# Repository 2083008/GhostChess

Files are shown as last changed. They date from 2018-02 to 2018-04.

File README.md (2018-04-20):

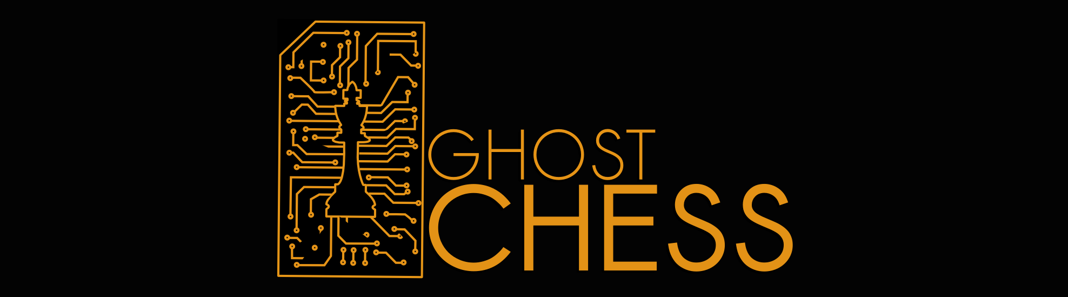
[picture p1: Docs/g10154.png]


Check us out on [Youtube](https://youtu.be/5MZTQNxuwCw) and [HACKADAY](https://hackaday.com/2018/04/19/play-chess-against-a-ghost/)

# team11_RTEP5: Mechanised User vs. Computer Chess Board
Computer chess engines have become very advanced and are great for learning how to play or for improving your skills. However, playing on a computer is just not the same as seeing the physical pieces move across the board!

This project aims to design and build a mechanised chess device, allowing users to play against the StockFish chess engine on a physical board. An X-Y positioning table will use an electromagnet to execute the computer-generated moves, moving the physical pieces across the board, mimicking a real chess expert.

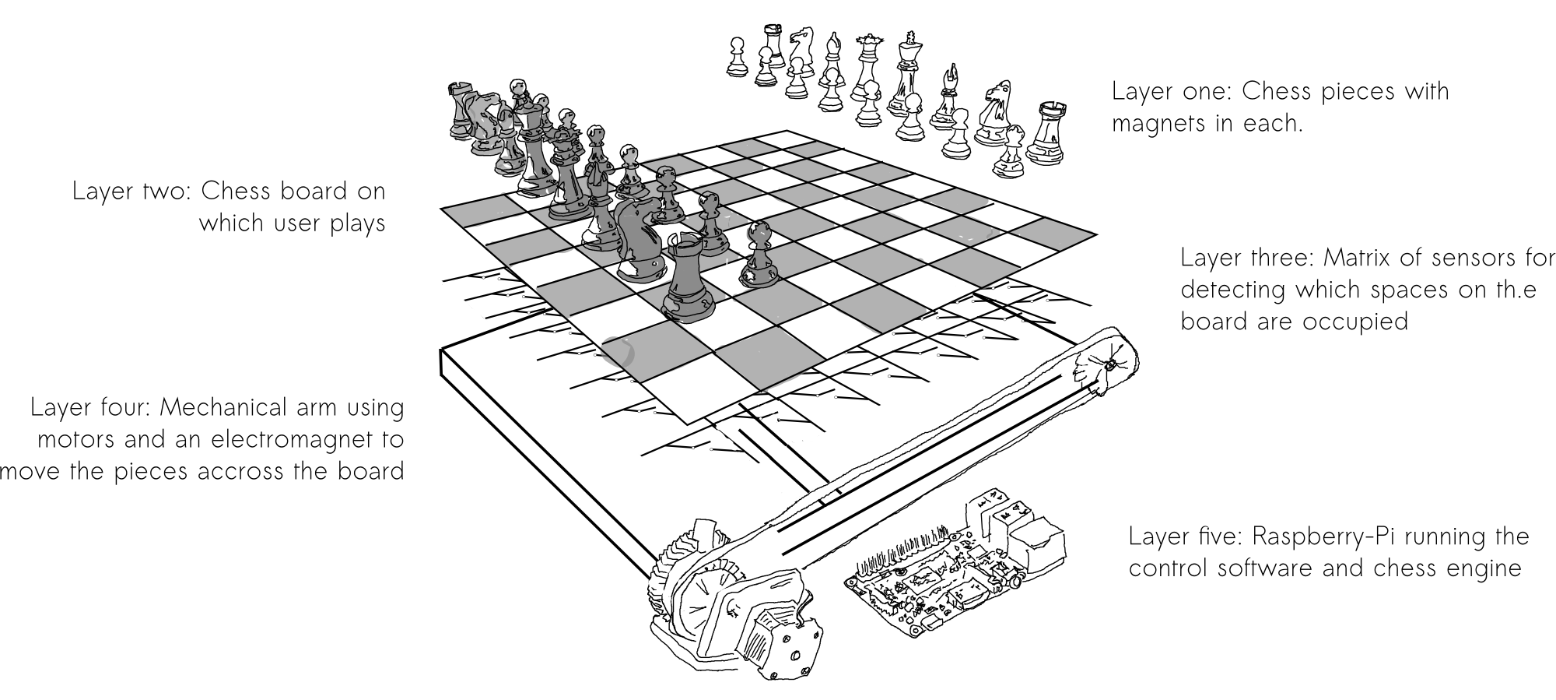
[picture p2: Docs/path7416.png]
Layers of the system


# Why?
Playing games on a computer screen can be great - but it takes away from the game. Ghost Chess allows users to detach from their everyday computer use to really invest in the game itself, providing a more engaging gaming experience. Variable difficulty levels allow users to improve their chess skills. Not to mention that it is really cool!

## Table of Contents
[Getting Started](#getting_started)
  * [Required Hardware](#required_hardware)
  * [Assembling the mechanical arm](#mechanical_arm)
  * [Building Software](#building_software)
  * [Motor Control](#motor_control)
  
[System Specification](#system_specification)

[Project Progress/Evaluation](#progress_evaluation)
  * [Team Roles](#team_roles)

[FAQ/Common Issues](#faq)

# Getting Started 
All project-related software can be found in folder "src", and all required schematics/CAD files/PCB designs/footprints are located in folder "Docs".
## Required Hardware 
* The full [Bill of Materials](goo.gl/mntyCQ): 
X-Y positioning:
* 3x Stepper Motors (Nema 17)
* 3x Stepper motor drivers (Pololu A4988)
* 1x Electromagnet (3/4' Diameter, 4.5kg pull force) and 40x Button Magnets (3mm diameter, 2mm height)
* P36NF06L FET
* 2x 700/900 mm plywood sheets
* 2x 700mm and 1x 500mm T-slot bar
* 3x 125mm oak shuttles
* 6x T-bolts
* 1x 500mm oak bar
* 6x 40T GT2 6mm Timing Pulley
* 5M 6mm GT2 fiber-glass re-enforced rubber timing belt
* 1x 500mm metal shaft and 1x 30mm metal shaft
* 6x Flanged Corner Bracket BZP

Sensor Matrix:
* 64x Latching Hall-effect Sensors (SS361RT) and 64 10kohm resistors
* 2x 8-1 FET Mux/Demux (SN74CBT3251)

Other:
* Laser-cut Acrylic chess board and 3D printed pieces
* Raspberry Pi 3 Model B

# Assembling the mechanical arm: 
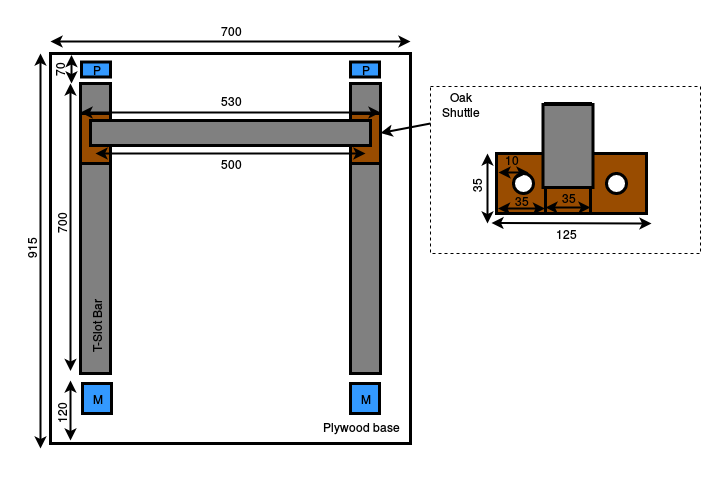
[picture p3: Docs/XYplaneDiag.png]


All measurements in mm.

A Plywood base is used to ensure that there is no unwanted lateral motion under tension. T-slot bars act as runners for oak shuttles, held in place by T-bolts. The Y plane movement is supported by two T-slot bars, each 700mm in length. Mounted to both the Oak shuttles on the Y plane is an oak bar which holds the 3rd, X plane, T-slot bar in place (500mm in length). Each shuttle is moved using a timing belt which is mounted through 2 pulleys to a stepper motor.

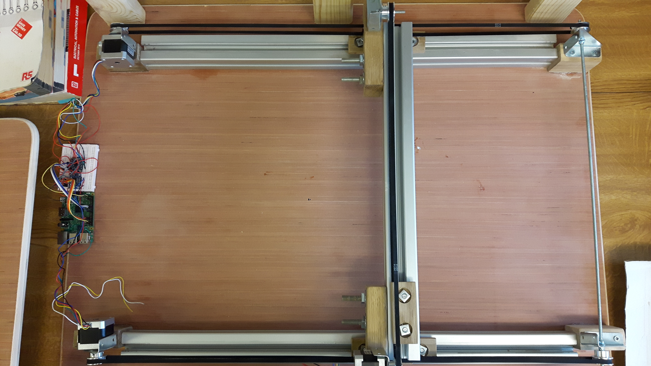
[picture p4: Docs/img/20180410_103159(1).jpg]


1. Cut and bevel the two 915mm/70mm Plywood sheets which form the base and top plate of the design
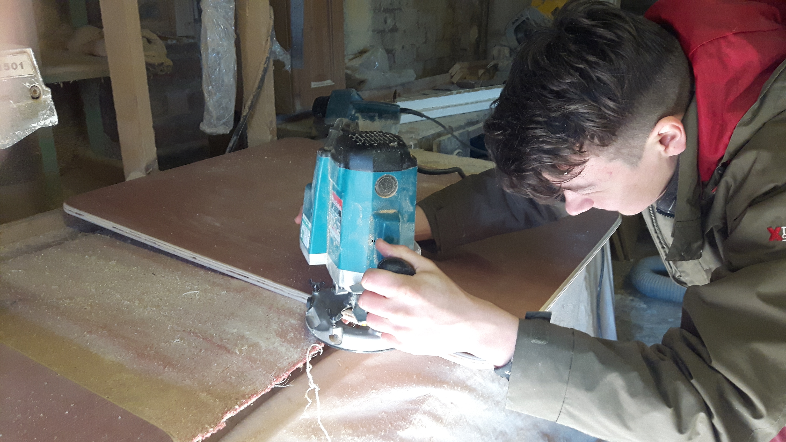
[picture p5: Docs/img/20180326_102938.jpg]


2. Bolt down the 2 700mm length T-slot bars through the base plywood sheet (4 bolts spaced evenly)
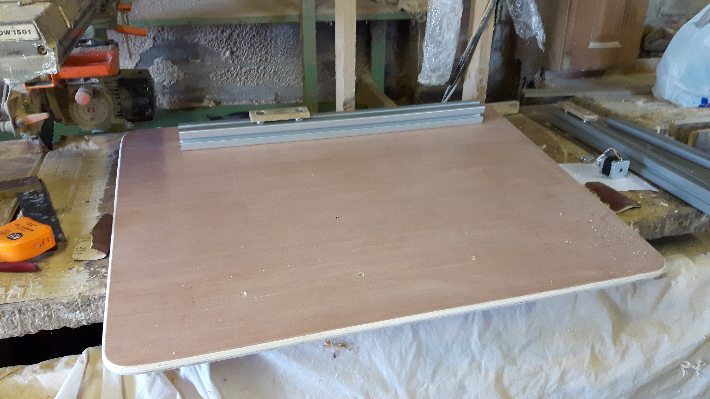
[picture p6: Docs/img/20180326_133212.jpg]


3. Cut the 3 125mm/35mm oak shuttles and the 500mm/35mm oak cross bar
4. Mount the oak cross bar to two of the oak shuttles using miter-fast bond and screws
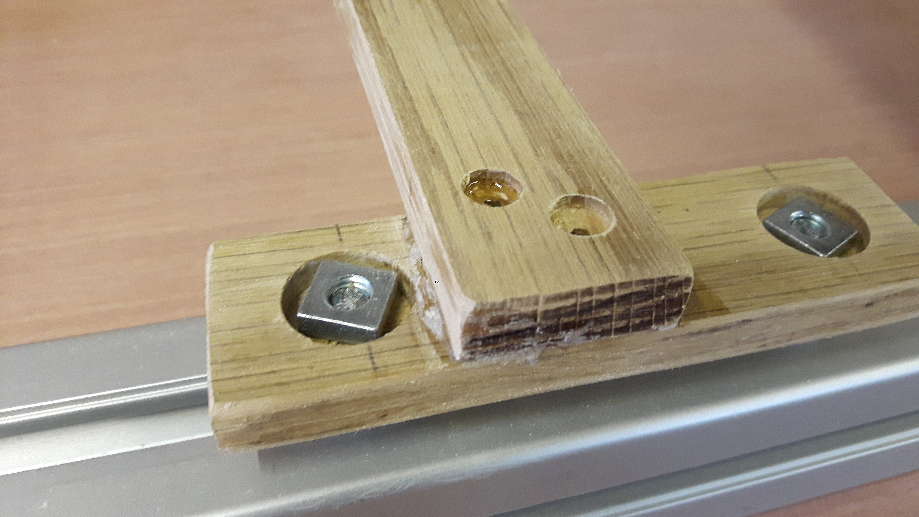
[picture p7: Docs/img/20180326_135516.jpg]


5. Bolt the 500mm T-slot bar to the oak cross bar (4 bolts spaced evenly)
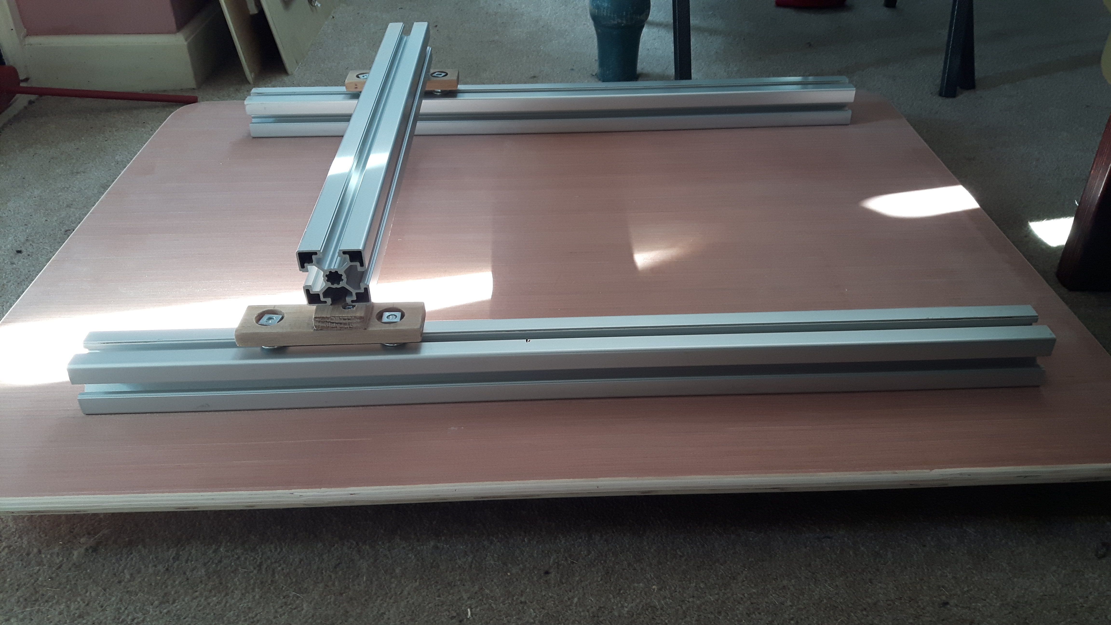
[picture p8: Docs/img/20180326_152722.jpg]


6. Cut oak blocks to stand the pulleys and motors (x6, 3 for motors and 3 for pulleys), plane to match heights (the bottom of the pulleys should be at the same height as the top of the oak shuttles to ensure that the timing belt can be fixed securely)
7. Fix the oak blocks to the plywood base using miter fast bond and screws
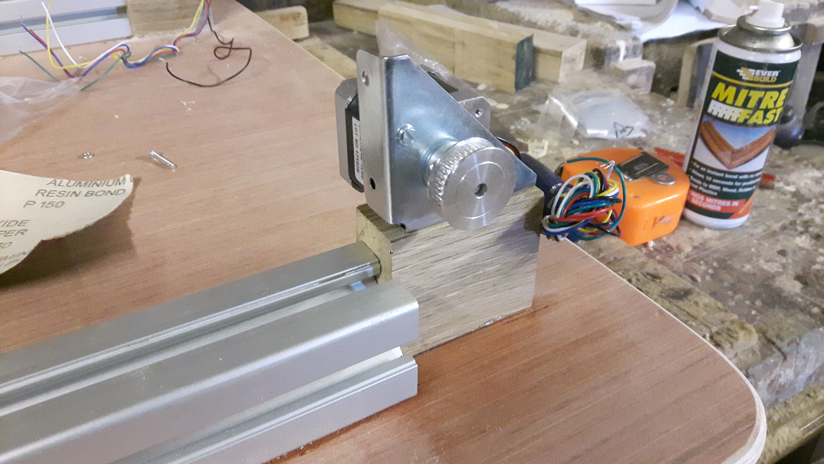
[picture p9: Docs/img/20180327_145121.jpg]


8. fix the flaged corner brackets to the oak blocks, ensuring they are parallel to the T-slot bar and in line
9. attach the motors to the flanged corner brackets by drilling holes in the corner bracket and bolting the motors through them
10. attach pulleys to motor shafts, 500mm metal shaft, and 30mm metal shaft


11. attach timing belt to oak shuttles through pulleys with tension using miter fast bond
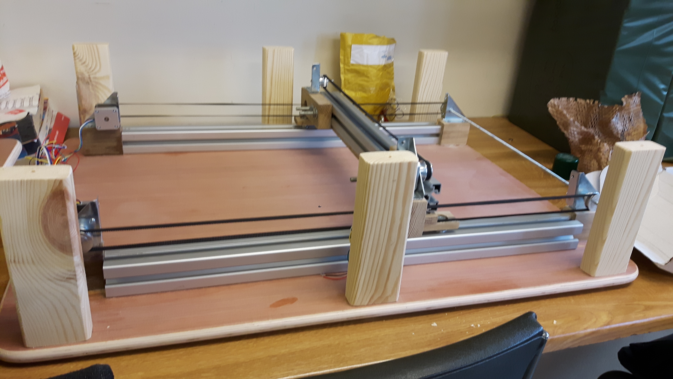
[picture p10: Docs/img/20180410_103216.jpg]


### Electromagnet

The electromagnet is controlled using a GPIO on the RASPI, connected to the gate of a N-Channel FET (P36NF06L) with a R10k to GND. 12V DC from the power supply connected Electromagnet with the other connection to the Drain of the FET and the Source to GND.

# Sensor matrix: detecting the users move
The sensor matrix is comprised of 64 latching (0/1 state will be preserved until reset) hall-effect (detecting magnetic field, turned on by a North magnetic pole and off by South magnetic pole) sensors, with one sensor below each square. The sensor (SS361RT) has three terminals - Supply voltage (V_cc), Output and Ground. The most basic circuit is created by connecting a resistor (10k recommended) between V_cc and Output - the transistor in the sensor would act like a short circuit when turned on (pulling the output to Ground), and as an open circuit when exposed to North magnetic pole (the resistor pulling the output to V_cc or 5V, when supplied from the RaspberryPi). More can be seen in the datasheet: https://sensing.honeywell.com/honeywell-sensing-latching-digital-hall-effect-sensor-ic-datasheet-ss361rt-ss461r-005901-3-en.pdf

To assemble the sensor matrix, follow the steps outlined below. Apart from the components mentioned in the beginning, you will need:
* Solder iron (possibly with a fine tip) and a large amount of solder;
* Long multi and single-core wires;
* Wire strippers;
* Hot glue gun and sticks;
* Cardboard and drawing instruments;
* Duct tape.

1. Copy the exact dimensions of the laser-cut acrylic board and draw lines through all square diagonals, so you find the exact center. Prepare your multi-core wire for the SMD hall-effect sensors:


2. Solder the sensor terminals to wires and start supergluing them to the cardboard, making sure they are positioned exactly in the center:
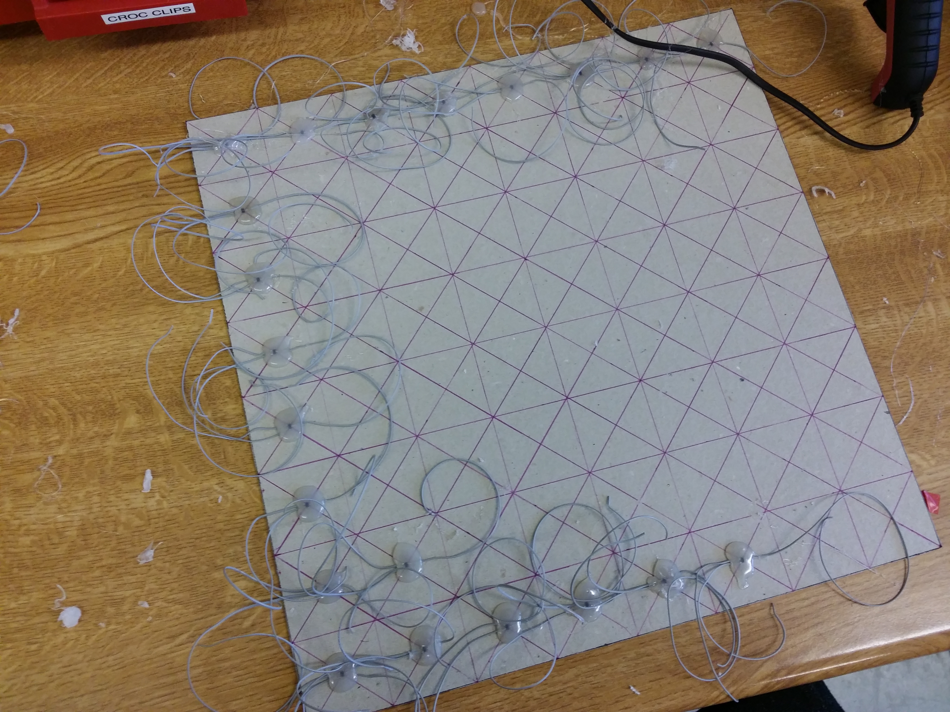
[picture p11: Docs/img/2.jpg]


3. After you have glued all sensors, trim the wires so you have working space:
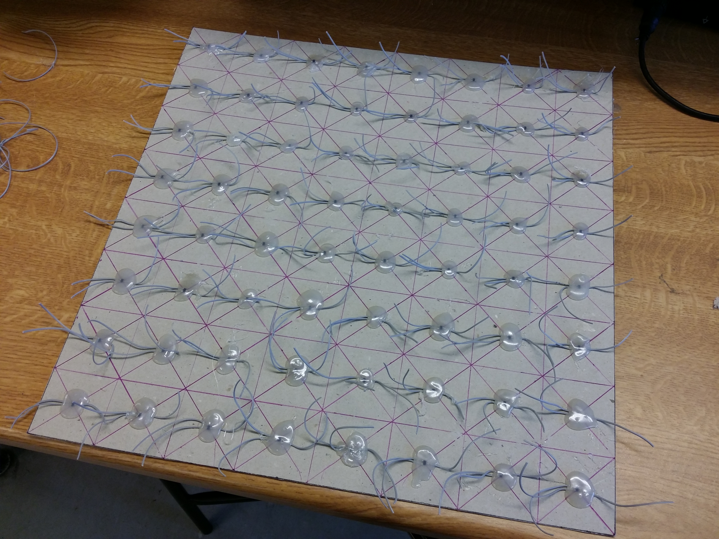
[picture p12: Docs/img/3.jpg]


4. Strip single-core wires, which will serve as "rails". Place them along each column line, starting from the side of the ground terminal. Solder the ground terminal sensor wires to the "ground net".
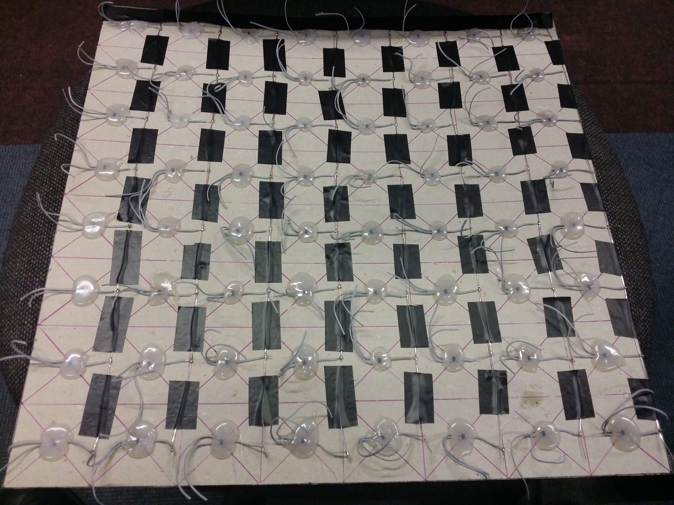
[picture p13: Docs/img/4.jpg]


5. Cover "ground net" with at least 2 layers of duct tape, then place 8 column wires (V_cc) in parallel with the ground wires. Cover the intersections with the rows with duct tape, and place 8 row wires (Output) along the row lines. 


6. Solder the resistors and corresponding sensor wires between the supply and output wire nets:
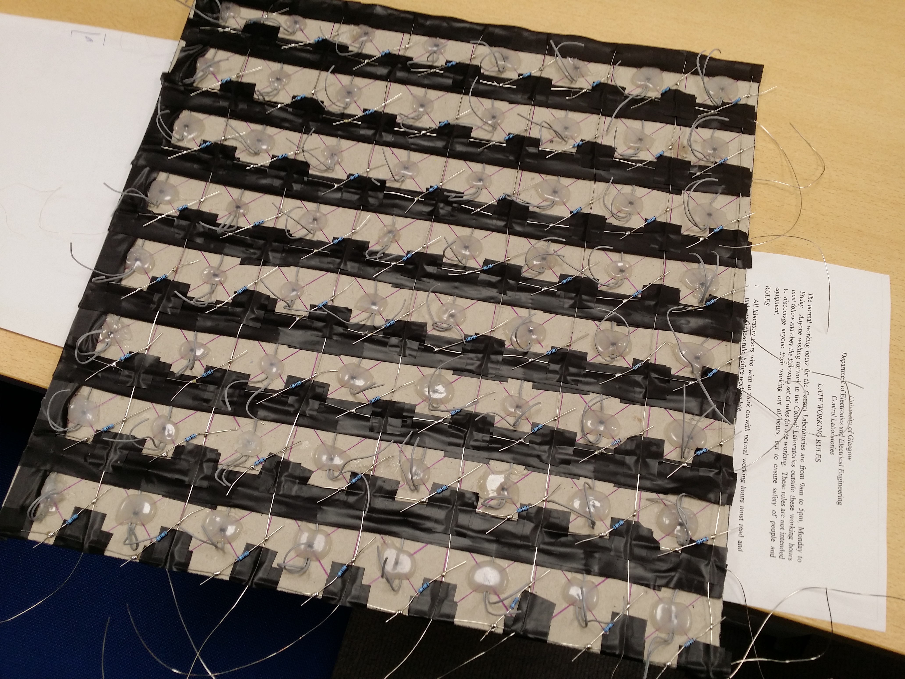
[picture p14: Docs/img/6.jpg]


7. Solder multi-core wires to the two multiplexer/demultiplexers and superglue the sensor, so the SMD legs would not break from bending.
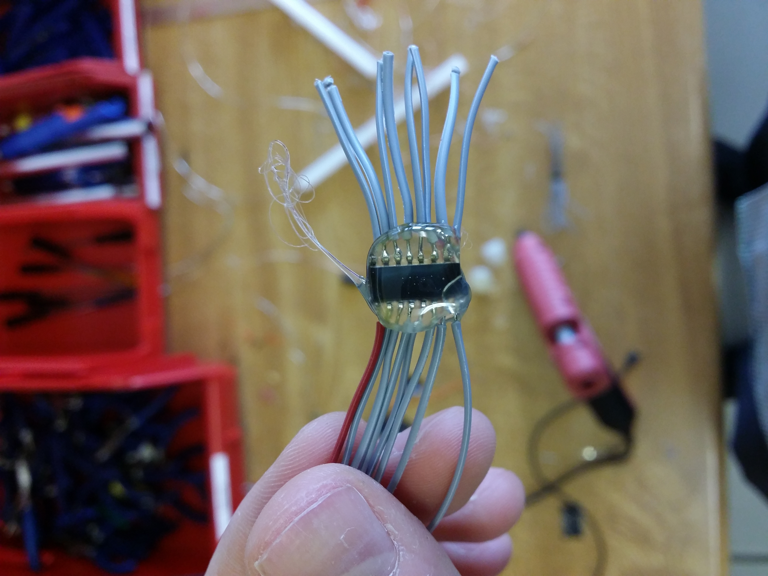
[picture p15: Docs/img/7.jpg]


Prior to connecting everything together, test the output of each hall-effect sensor using a magnet, by iteratively supplying voltage to each column and reading each row. The circuit for the matrix can be seen in Docs/PCB/sensor_array.pdf. Bear in mind that the sensing part of this project is still in alpha.

The Bill of Materials for this project can be seen here: https://docs.google.com/spreadsheets/d/1Xdm7poSaMNww_U4s14YsQG5IgNS09zYjubY1kuaMT44/edit?usp=sharing

# Building Software 
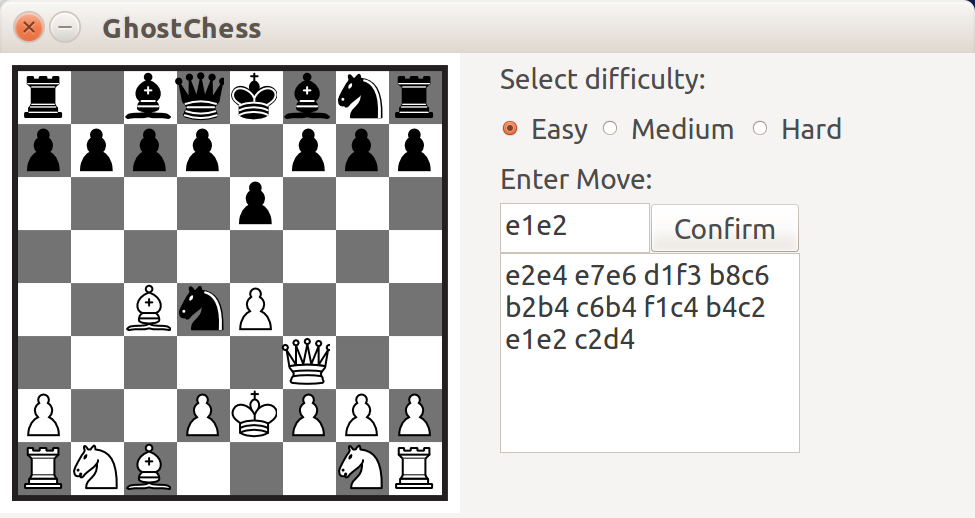
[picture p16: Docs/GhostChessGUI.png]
GUU

To build this project's software: first clone the repository then run

```
cd GhostChess
cmake .
make

./GhostChess

```
**NB** Requires QT5, to install:
```
sudo apt-get install qt-5 default
```
Moves can be entered through the GUI or through the CLI (both entered in Algerbraic Chess Notation eg e2e4...).
## Software Flow:

The software forms an interface between the user and the StockFish API, updating the API with new moves and reading out the computers moves to pass to the motor control software. A full software flow diagram can be found in [Docs/Software_flow_diagram](Docs/Software_flow_diagram.png).

## Motor control: 

Motor control is performed using digital GPIO outputs which control the Pololu A4988 stepper motor driver. The stepper motors are rotated in 4 stages which relates to 4 configurations of the H-bridge inductor which is used to turn the motor shaft. A single rotation therefore relates to:

To move pieces accross the board the control software performs the following steps:
1. Move to coordinate y1 x1 (the coordinate of the piece to be moved)
2. Turn on electro magnet
3. Move to edge of square (to ensure that the peice being moved will not collide with any pieces in surrounding squares)
4. Move to coordinate y2 x2 (the space to be moved to)
5. Return piece to the centre of the square
6. Return to origin of the board (located at square A1)

# System Specification 

Responsiveness of the system. How long the system will take to move a piece.
Latency permitted for the piece -> dependant on where the piece has to move (
Sampling rate of 2Hz for board state of 64 elements.
Thread will poll the board every 2Hz and check for changes/validate and make sure user has moved a piece correctly then the engine will respond.
Bus Protocol, communicating to motor drivers.
Channels? 1
Kernel space usage was not deemed necessary since the latencies were in the order of seconds/ms. For simpicity and faster development time then staying in user space was preferred.
Data flow  is shown in the [software diagram](Docs/Software_flow_diagram.png) (formats, latencies, processing and conversions)
Buffers for the move history of the game as well as the engines returned moves are stored.
 
Threads operate for fetching the user input for the CLI as well. The board array will also be updated using a thread executed at 2Hz.

### Team Roles 
* Alex Angelov - 3D Pieces Modelling, Board Production, Position Sensing and Related Software
* Tim Ness - Design Assembly, Accurate Motor Control and Related Software
* Alex Smith - Chess Engine Integration and QT GUI Interface

# Progress Success Evaluation 
Issue tracking and Project Tracking through github's associated tools.

How does the project acheive the goals that are set out above?

# FAQ/Common Issues 
**Q:** QLabel: No such file or directory

**A:** QT5 must be installed to build the software, run  ```sudo apt-get install qt-5 default ```

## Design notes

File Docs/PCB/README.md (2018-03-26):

THis is the documentation for replicating the PCB created for the GhostChess Project

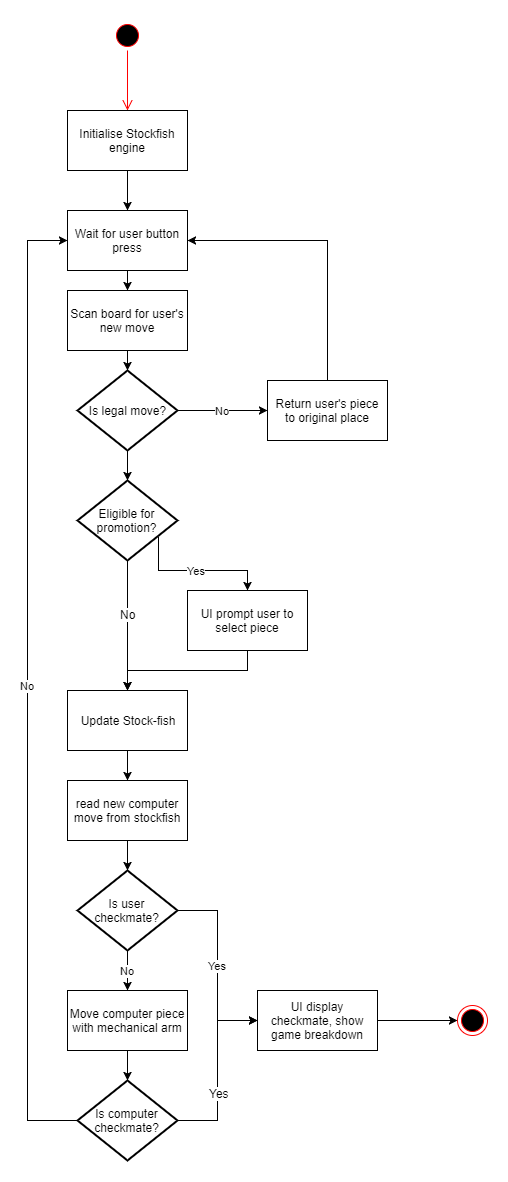
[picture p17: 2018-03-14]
Docs/Software_flow_diagram.png

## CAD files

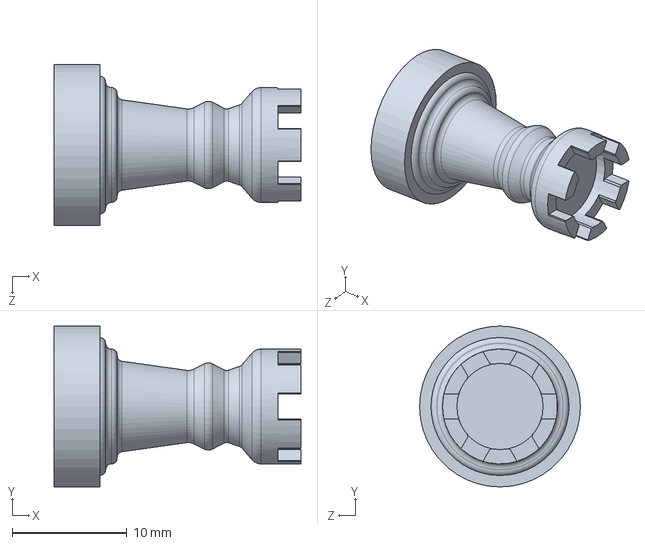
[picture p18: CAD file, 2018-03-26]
Docs/CAD-Mechanical/chess_pieces/ROOK.SLDPRT
21.5 x 14.0 x 14.0 mm

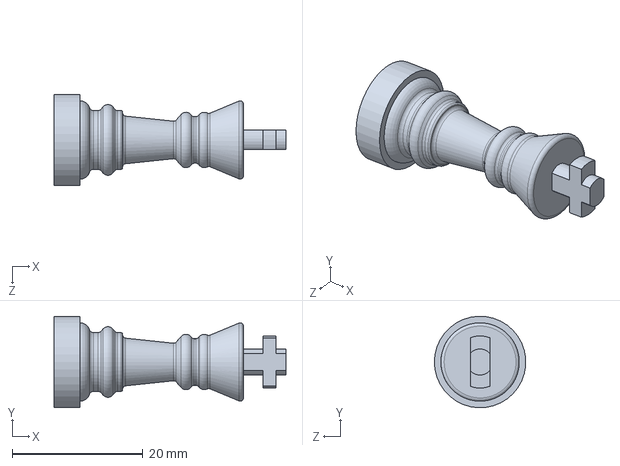
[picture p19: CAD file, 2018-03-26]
Docs/CAD-Mechanical/chess_pieces/KING.SLDPRT
35.5 x 14.0 x 14.0 mm

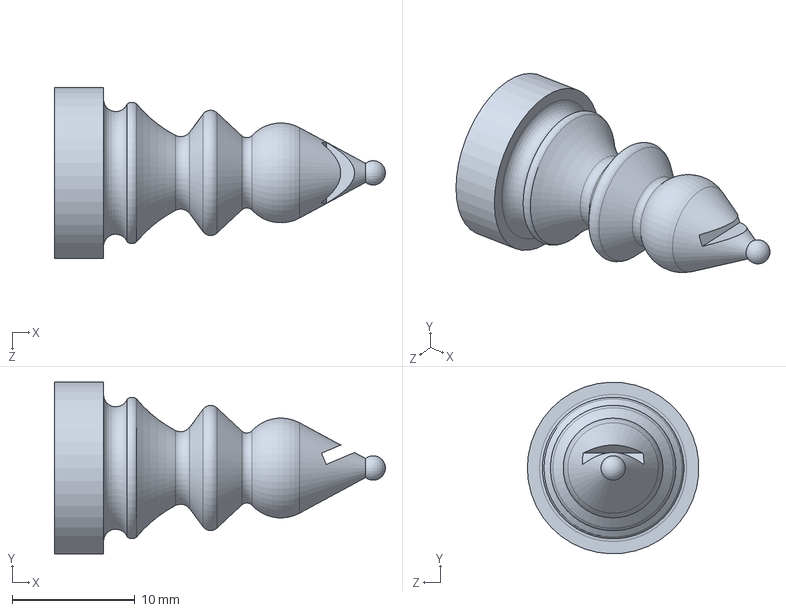
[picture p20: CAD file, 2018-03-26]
Docs/CAD-Mechanical/chess_pieces/BISHOP.SLDPRT
27.0 x 14.0 x 14.0 mm

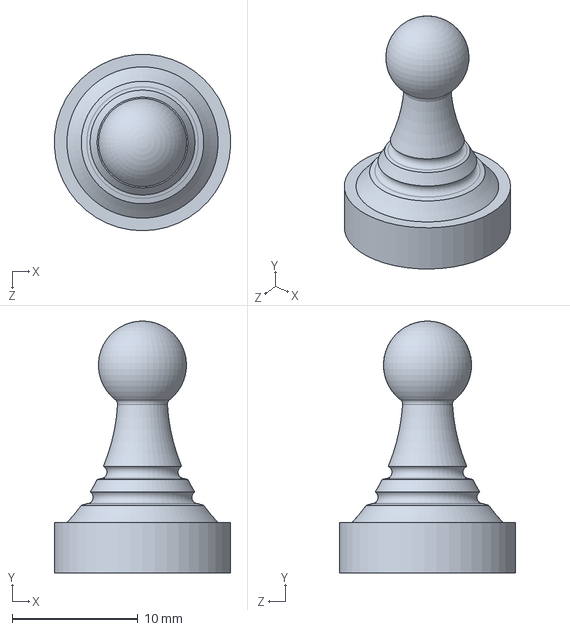
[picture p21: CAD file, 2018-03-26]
Docs/CAD-Mechanical/chess_pieces/PAWN.SLDPRT
14.0 x 20.0 x 14.0 mm

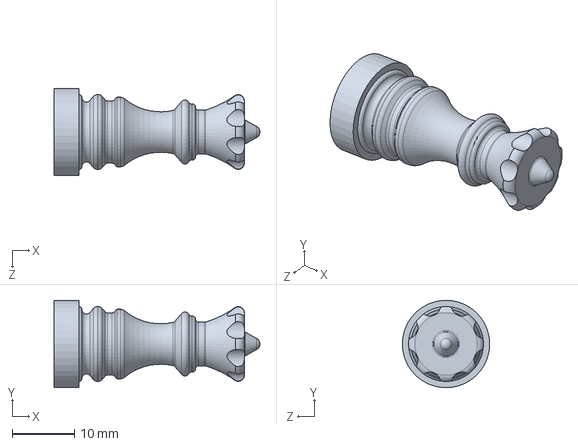
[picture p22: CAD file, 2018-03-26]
Docs/CAD-Mechanical/chess_pieces/QUEEN.SLDPRT
33.0 x 14.0 x 14.0 mm

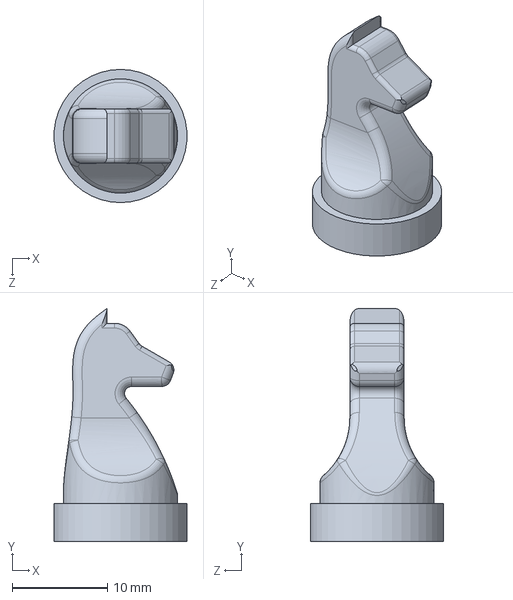
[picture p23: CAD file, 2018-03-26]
Docs/CAD-Mechanical/chess_pieces/KNIGHT.SLDPRT
14.0 x 24.5 x 14.0 mm

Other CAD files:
Docs/CAD-Mechanical/chess_board/chess_board.SLDPRT
Docs/CAD-Mechanical/chess_board/chess_board.DXF
Docs/CAD-Mechanical/chess_pieces/BISHOP.STL
Docs/CAD-Mechanical/chess_pieces/KING.STL
Docs/CAD-Mechanical/chess_pieces/KNIGHT.STL
Docs/CAD-Mechanical/chess_pieces/PAWN.STL
Docs/CAD-Mechanical/chess_pieces/QUEEN.STL
Docs/CAD-Mechanical/chess_pieces/ROOK.STL

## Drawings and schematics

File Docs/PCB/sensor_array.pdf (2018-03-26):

# M2 SN74CBT3251D VCC ¹⁶ GND

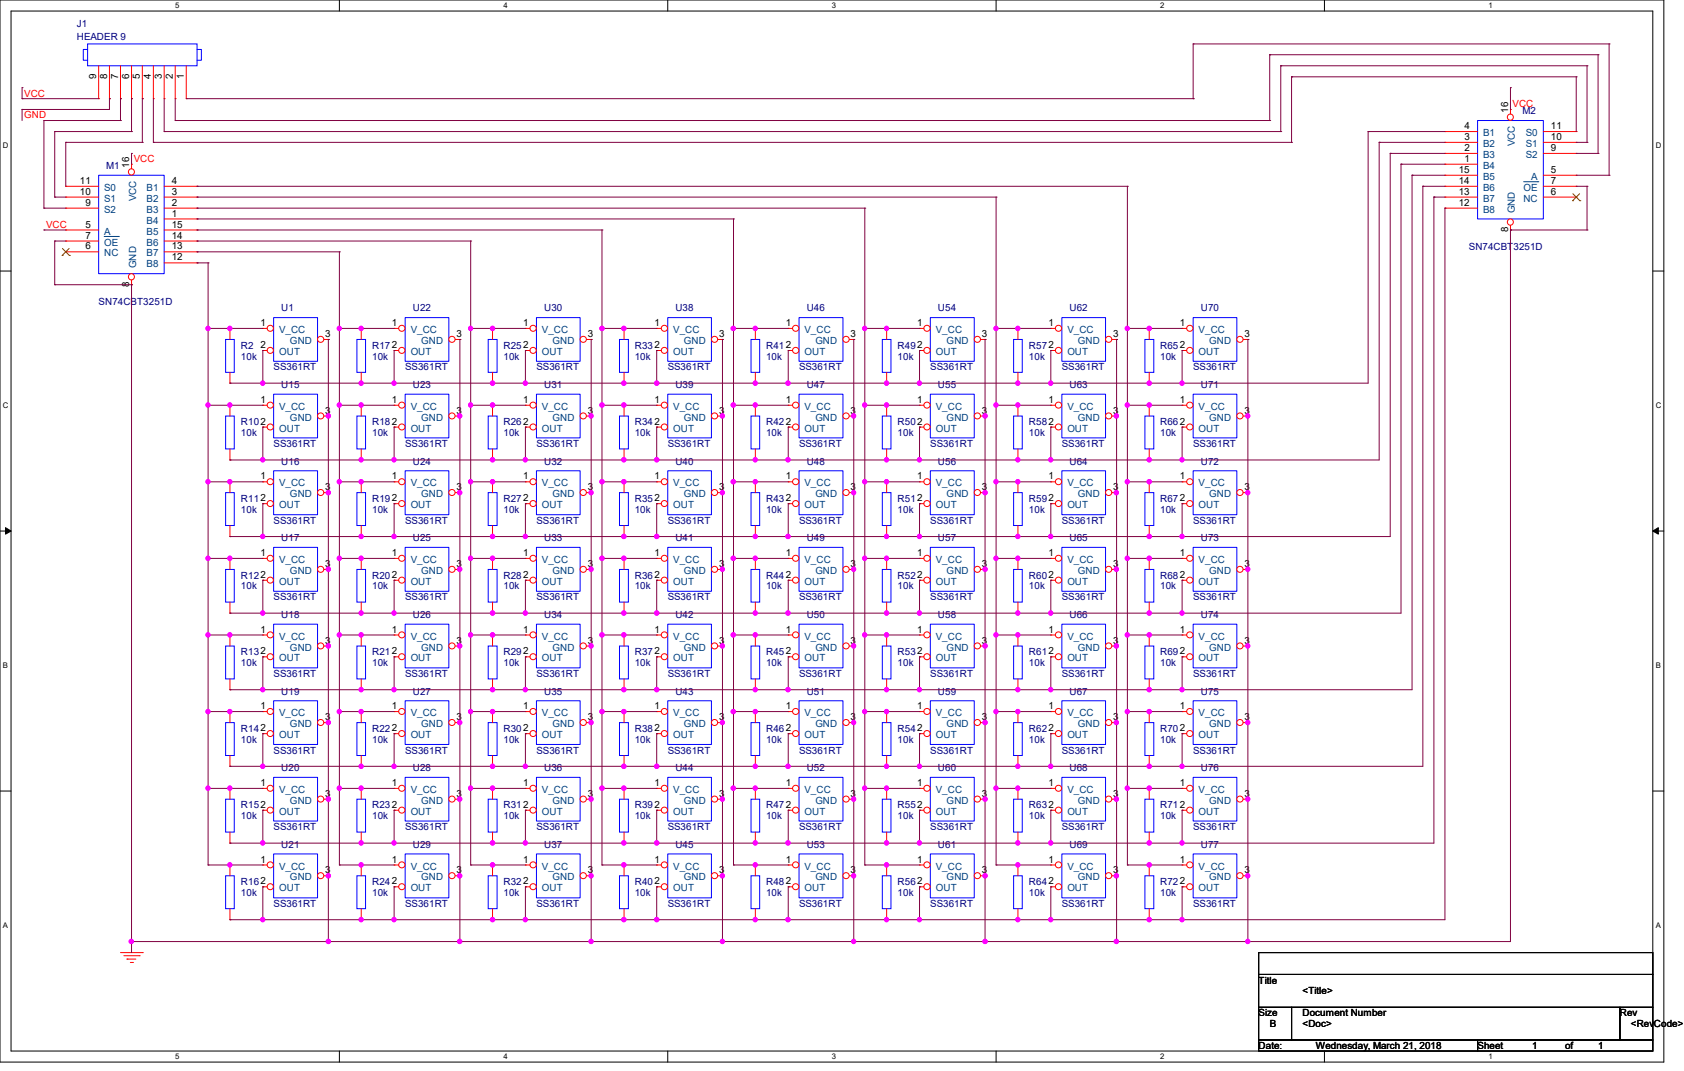
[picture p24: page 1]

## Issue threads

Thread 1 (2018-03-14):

Hardware info

npes-95, 2018-03-14:
Would be great to see how the hardware works? Could you upload some PCB schematics/block diagrams?

- Team 4

2083008, 2018-03-26:
Added schematics for the board array and more to follow. Video will be added soon. Cheers!

Closed 2018-03-26.

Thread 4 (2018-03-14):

About the electromagnetic

Kenny840394191, 2018-03-14:
Using the magnets to control the chess is a good idea, but how do you ensure that electromagnetic interactions do not affect each other because the distance between the pieces is very close. And how to prevent wrong move?

team 15

2083008, 2018-03-26:
We have tried several different magnets to find a balance between magnetic force and size, also ensuring a sufficiently large board so they do not interfere when moving a piece. There is software being written to check valid moves! Cheers

Closed 2018-03-26.

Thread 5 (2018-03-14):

More Hardware Information Required

2077762b, 2018-03-14:
This is perhaps the most challenging project. I am excited to see how it turns out. Just a few issues to consider:
* It would be great if some PCB design files were added to the repository to help someone replicate the project.
* There appears to be minimal commentary in the code. It would be great if each C++ member function had a comment explaining its purpose.
* Currently it would be extremely difficult to replicate this project. Much further information is required in the README and Wiki sections, particularly explaining the mechanical assembly.

**Team 10**

2083008, 2018-03-26:
- Added schematics for the sensory array as well as more documentation
- Added some more comments to the code
- Further help provided for setup of this project as well as section for FAQ/Common issues as these are discovered

Cheers

Closed 2018-03-26.

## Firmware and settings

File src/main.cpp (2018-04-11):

#include "main.h"
#include "MainWindow.h"

char board[8][8];

//constants
//#define X_OFFSET 12
//#define Y_OFFSET 385
//#define IMAGE_SIZE 54

namespace PSQT
{
void init();
}

//buffer that will be updated by the chess engine
std::string best_move_buffer;
// buffer to store move history of the game
std::string move_history;

void stockfishInit();
// returns a=1 b=2...
int charToInt(char val);
void parse_input(Board* pboard, QTextEdit* move_box);
void runEngine(const char* moves);

int main(int argc, char **argv)
{

    // Initialise the Stockfish chess engine
    stockfishInit();

    std::cout << "GhostChess V_0.1" << std::endl;

    QApplication myapp(argc, argv);
    MainWindow mainWin;
    MainWindow* pmainWin = &mainWin;
    Board* test = new Board(pmainWin);
    mainWin.setBoard(test);

    std::thread t1 = std::thread(parse_input, test,pmainWin->move_box);
    mainWin.show();
    return myapp.exec();   
}

void runEngine(const char* moves)
{
    char setup[100] = "position startpos moves ";
    const char *argse[4] = {"uci", strcat(setup, moves), "isready", "go"};
    
    //silence cout from the engine
    std::cout.setstate(std::ios_base::badbit); 
    // Run the engine
    UCI::loop(4, argse);
    Search::clear(); // Join the best move search threads

    std::cout.clear(); // reenable cout
    std::cout << "Engines Move -> "<< best_move_buffer << std::endl;

}

void stockfishInit()
{
    //std::cout << engine_info() << std::endl;
    UCI::init(Options);
    PSQT::init();
    Bitboards::init();
    Position::init();
    Bitbases::init();
    Search::init();
    Pawns::init();
    Tablebases::init(Options["SyzygyPath"]);
    TT.resize(Options["Hash"]);
    Threads.set(Options["Threads"]);
    Search::clear(); // After threads are up
}

// function for thread to parse user input for CLI
void parse_input(Board* pboard, QTextEdit* move_box)
{   
    std::cout << "Enter a move in Algebraic Notation (E.g e2e4) or q to quit " << std::endl;
    for (std::string line; std::getline(std::cin, line);) {
        if(line == "q"){
            //std::terminate(); should terminate the thread/join
            return;
        }
        
        if(line.length()!=4) {
            std::cout << "Invalid input!" << std::endl;
            
        } else {
            move_history.append(line);
            move_history.append(" ");
            move_box->append(QString::fromStdString(line));

            int tempy_start = line[1] - '0' -1;
            int tempy_end = line[3] - '0' -1;
            pboard->move(position{charToInt(line[0]),tempy_start},
                        position{charToInt(line[2]),tempy_end});
            
            const char* cmoves = move_history.c_str();
            std::cout << "Move List -> " << cmoves << std::endl;
            runEngine(cmoves);

            // BLACK MOVE
            int tempy_startb = best_move_buffer[1] - '0' -1;
            int tempy_endb = best_move_buffer[3] - '0' -1;
            pboard->move(position{charToInt(best_move_buffer[0]),tempy_startb},
                        position{charToInt(best_move_buffer[2]),tempy_endb});
            move_history += best_move_buffer;
            move_history += " ";
            move_box->append(QString::fromStdString(best_move_buffer));
            
        }
    }
}

int charToInt(char val)
{
    int tmp = val;
    return tmp-97; // 97 to get a = 0, b = 1 etc..
}

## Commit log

2018-02-15 printing in correct (row,col) format
2018-03-04 print out FEN notation of board
2018-03-14 added software flow diagram
2018-03-16 pieces and board assets for the gui
2018-03-16 added all pieces for the gui board
2018-03-26 Sensory array schematic
2018-03-26 Added Sensory Array orcad files
    [DESIGN3.DSN]
2018-03-26 Upload of X-Y arm measurement diagram
2018-04-01 created board object with pointers to ChessPieces
2018-04-02 creating pieces for the board and storing them in a 2d array
2018-04-02 full board setup using qt
2018-04-09 playable chess through the CLI where the engine moves against the user, TODO tidy up prints and move method
2018-04-09 tidied up CLI, disabling the prints from Stockfish
2018-04-15 added images of full assembly stuff
2018-04-15 added images of the complete assembly with timing belts attached
